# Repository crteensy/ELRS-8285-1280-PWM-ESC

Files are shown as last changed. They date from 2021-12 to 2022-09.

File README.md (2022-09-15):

# ELRS-8285-1280-PWM-ESC
A 2.4 GHz ELRS resceiver with 4 PWM outputs and a 1S, 5A ESC

### Revision 1.1
- should now be more robust with two servos on one channel through a Y cable
 - adjusted pull-up value on PWM1
 - added pull-up on PWM2
- this required a minor layout change for the added pull-up

### Overview:
- 2.4 GHz ExpressLRS receiver, ESP8285 based, with WiFi antenna
- 4 Servo PWM outputs
- on-board ESC
 - Up to 5.5 V input voltage (1S LiPo or HV-LiPo)
 - BLHeli_S I_H_40 (I didn't test if deadtime can be reduced - it probably can)
 - Handled 5 A for over a minute on the bench without damage: bench power supply set to 4.5 V, Mamba 1408 4000KV, HQProp DP 4x3x3. There was a cover over the ESC to reduce airflow from the prop.
- Voltage divider to measure battery voltage (not yet supported by ExpressLRS, 20211230)
- Testpads to flash ESC firmware through the EFM8's UART - can also be used with an external flight controller and serial passthrough to configure the ESC and re-flash it
- ExpressLRS can be flashed through the servo header

RCGroups discussion thread: https://www.rcgroups.com/forums/showthread.php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

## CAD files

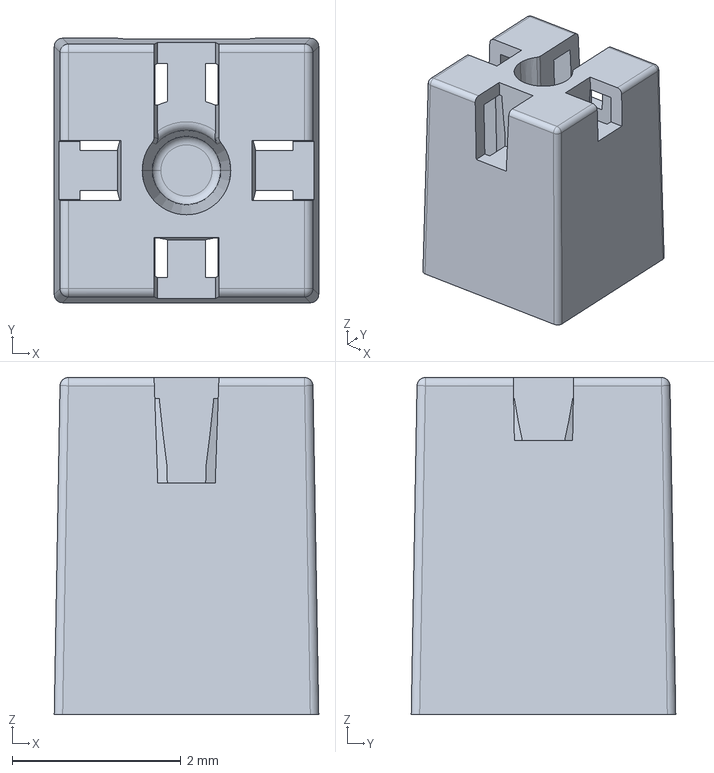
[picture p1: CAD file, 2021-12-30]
3d_local/479480001.stp
3.14 x 3.14 x 4.00 mm

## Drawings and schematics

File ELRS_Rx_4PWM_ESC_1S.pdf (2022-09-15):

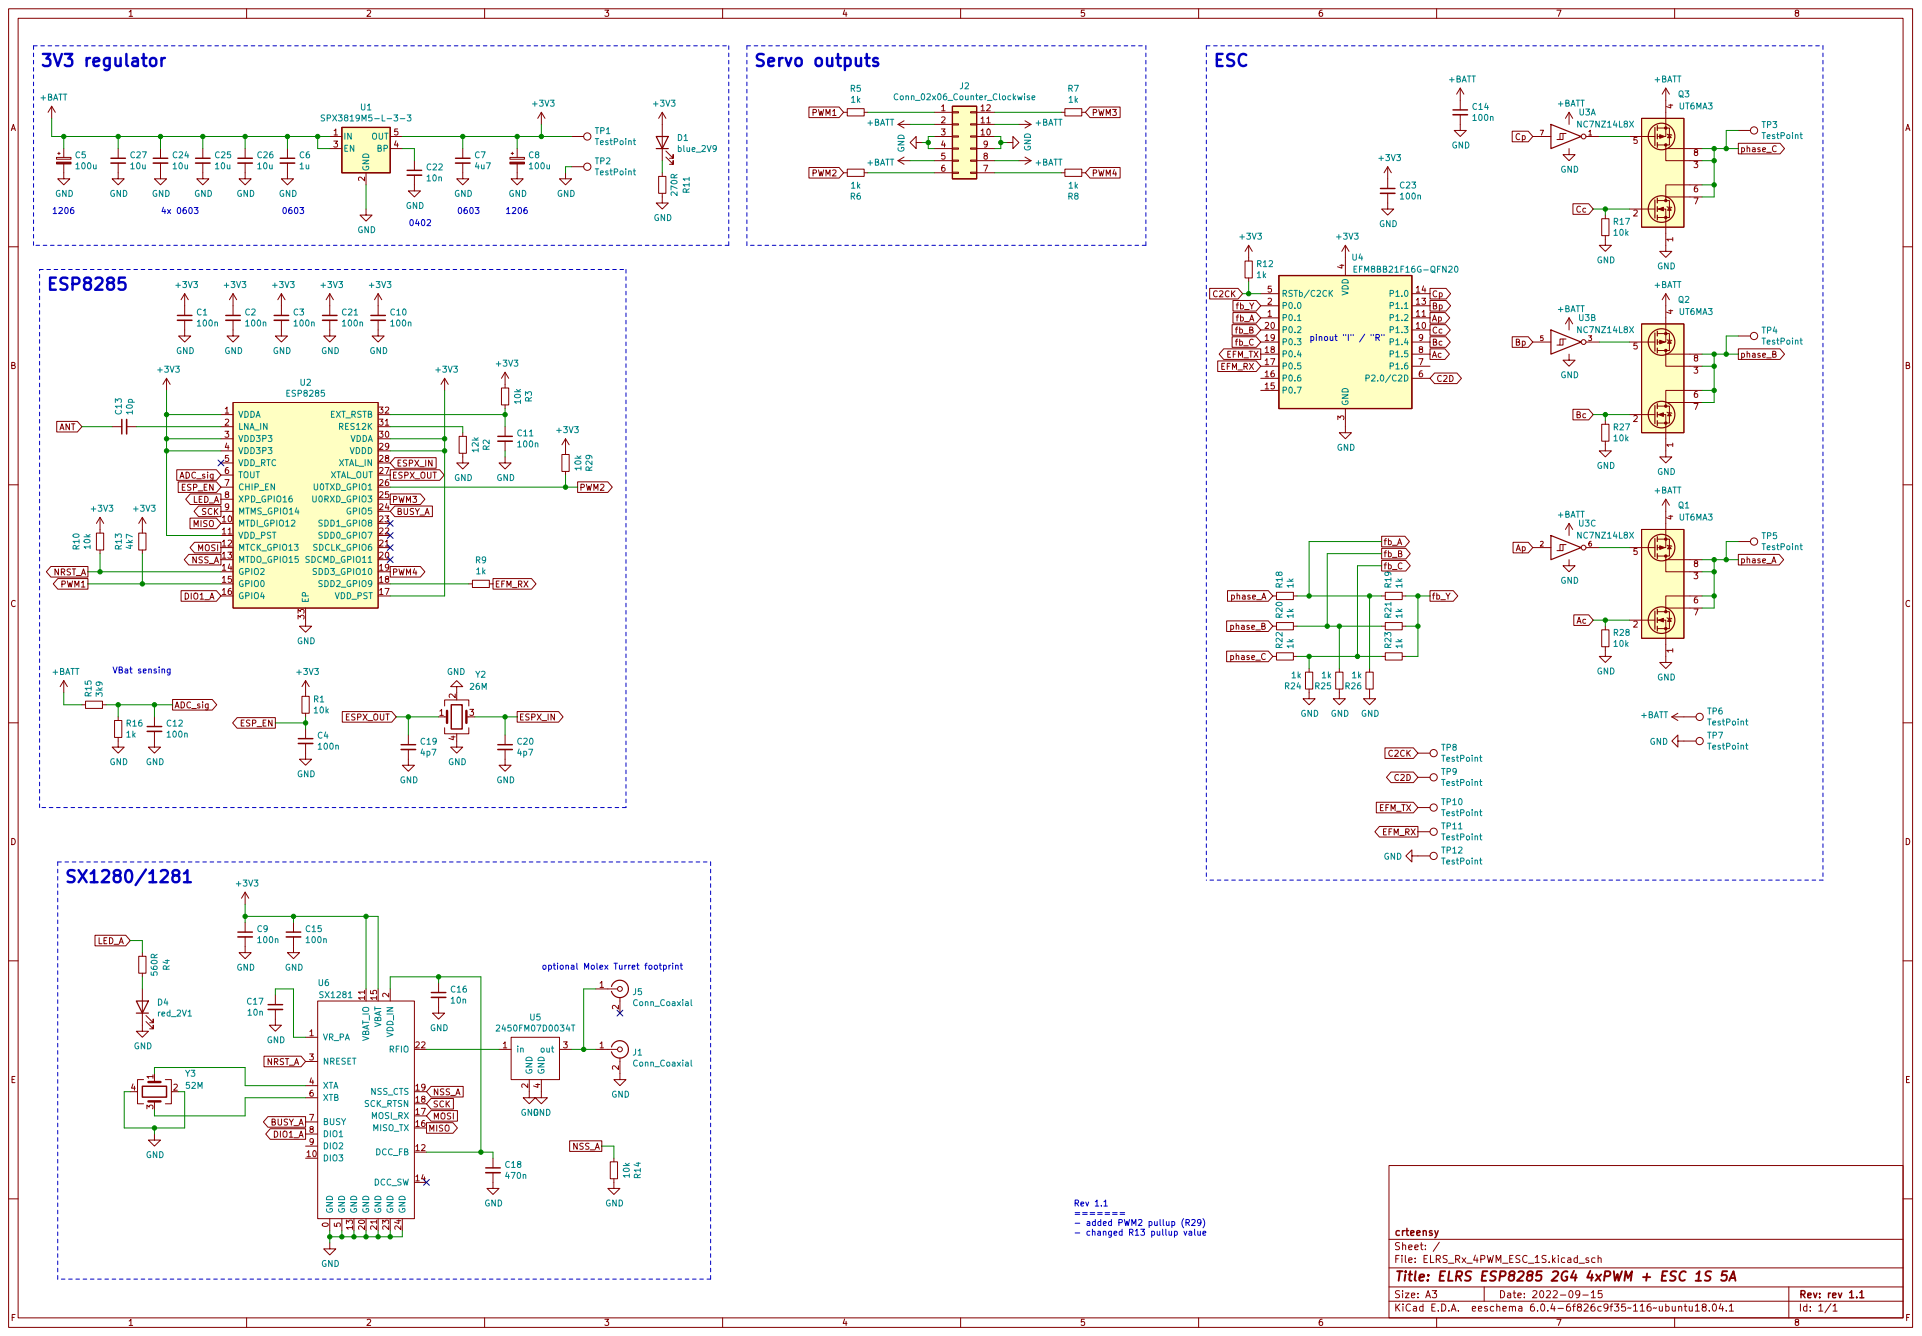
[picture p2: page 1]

optional Molex Turret footprint

2 GND 20 GND 21 RFIO 22 GND 23 GND 24 NRESET 3 XTA 4 GND

Id: 1/1 Title: ELRS ESP8285 2G4 4xPWM + ESC 1S 5A

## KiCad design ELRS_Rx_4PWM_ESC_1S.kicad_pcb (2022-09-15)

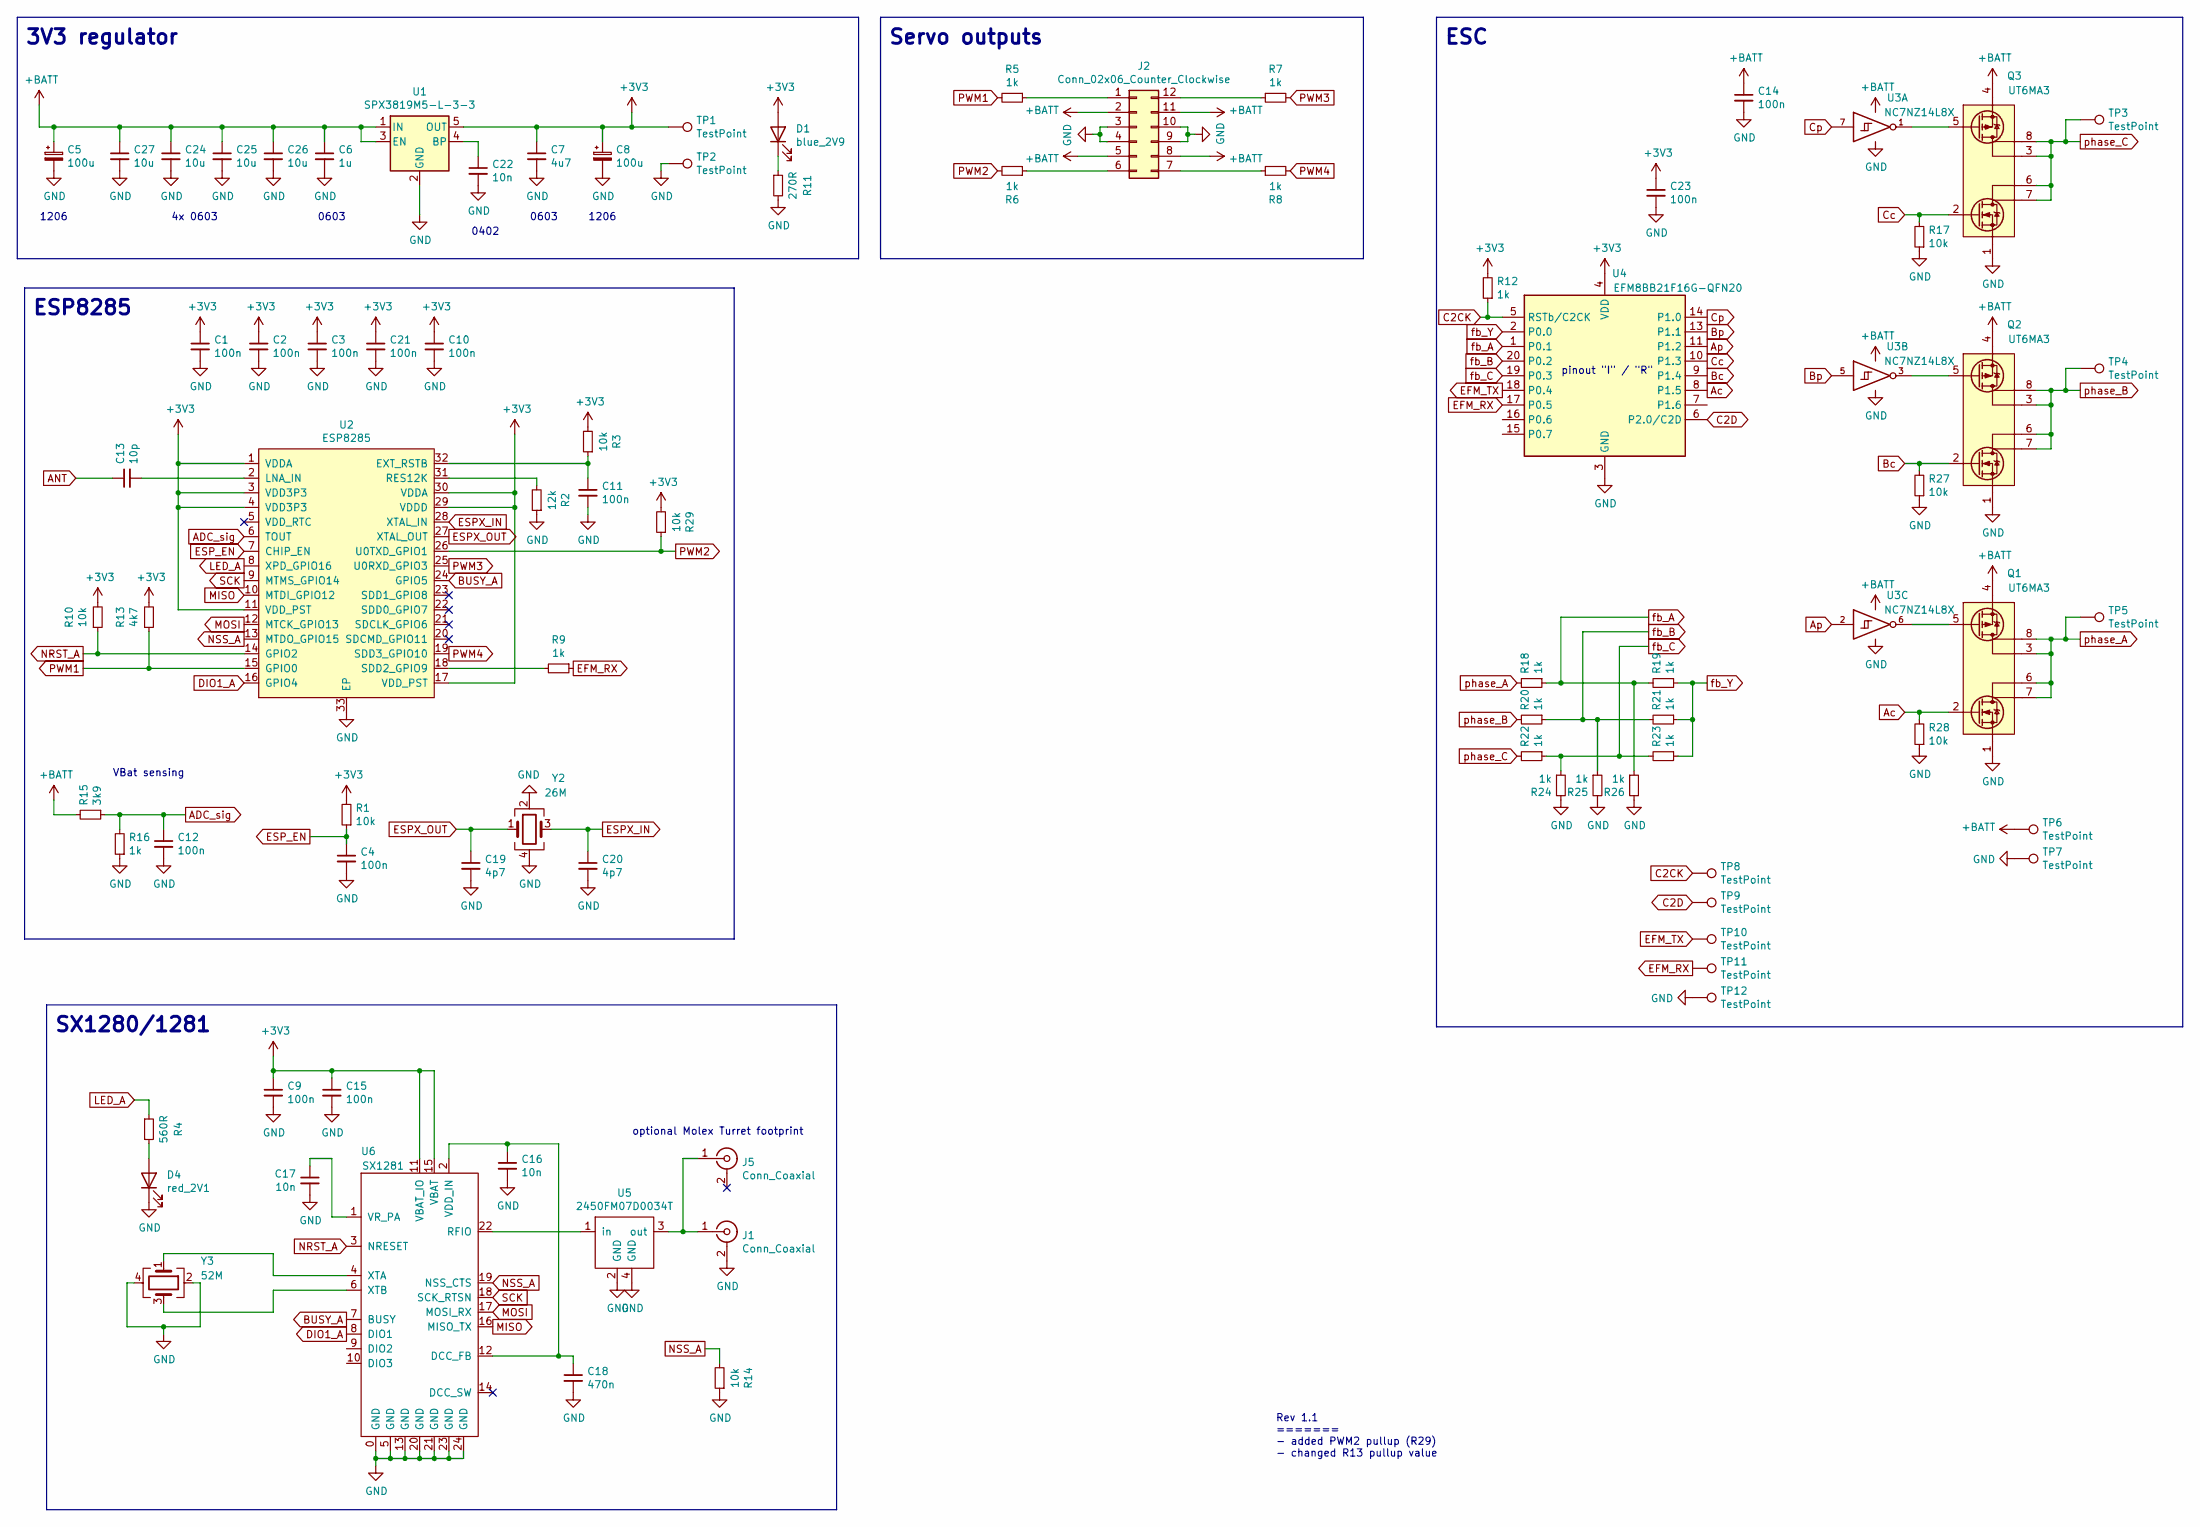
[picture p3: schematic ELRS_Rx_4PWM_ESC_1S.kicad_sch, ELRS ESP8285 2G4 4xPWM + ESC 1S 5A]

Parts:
C1, C2, C3, C4, C9, C10, C11, C12, C14, C15, C21, C23: 100n; C_0402_1005Metric
C5, C8: 100u; CP_EIA-3216-18_Kemet-A
C6: 1u; C_0603_1608Metric
C7: 4u7; C_0603_1608Metric
C13: 10p; C_0402_1005Metric
C16, C17, C22: 10n; C_0402_1005Metric
C18: 470n; C_0402_1005Metric
C19, C20: 4p7; C_0402_1005Metric
C24, C25, C26, C27: 10u; C_0603_1608Metric
D1: blue_2V9; LED_0402_1005Metric
D4: red_2V1; LED_0402_1005Metric
J1: Conn_Coaxial; U.FL_Molex_MCRF_73412-0110_Vertical_dense
J2: Conn_02x06_Counter_Clockwise; BoardEdge_Servo_4
J5: Conn_Coaxial; molex_479480001_2g4-turret
Q1, Q2, Q3: UT6MA3; DFN-6-2EP_2x2mm_P0.65mm_EP2x0.9x0.7
R1, R3, R10, R14, R17, R27, R28, R29: 10k; R_0402_1005Metric
R2: 12k; R_0402_1005Metric
R4: 560R; R_0402_1005Metric
R5, R6, R7, R8, R9, R12, R16, R18, R19, R20, R21, R22, R23, R24, R25, R26: 1k; R_0402_1005Metric
R11: 270R; R_0402_1005Metric
R13: 4k7; R_0402_1005Metric
R15: 3k9; R_0402_1005Metric
TP1, TP2, TP8, TP9, TP10, TP11, TP12: TestPoint; TestPoint_Pad_D1.0mm
TP3, TP4, TP5, TP6, TP7: TestPoint; TestPoint_Pad_2.5x2.5mm
U1: SPX3819M5-L-3-3; SOT-23-5
U2: ESP8285; QFN-32-1EP_5x5mm_P0.5mm_EP3.7x3.7mm_dense
U3: NC7NZ14L8X; UQFN-8_1.6x1.6mm_P0.50mm
U4: EFM8BB21F16G-QFN20; SiliconLabs_QFN-20-1EP_3x3mm_P0.5mm_EP1.8x1.8mm
U5: 2450FM07D0034T
U6: SX1281; QFN-24-1EP_4x4mm_P0.5mm_EP2.6x2.6mm_SX1280_dense
Y2: 26M; Crystal_SMD_2016-4Pin_2.0x1.6mm
Y3: 52M; Crystal_SMD_2016-4Pin_2.0x1.6mm

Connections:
+3V3: C1.1, C2.1, C3.1, C7.1, C8.1, C9.1, C10.1, C15.1, C21.1, C23.1, D1.2 (A), R1.2, R3.2, R10.2, R12.2, R13.2, R29.2, TP1.1, U1.5 (OUT), U2.1 (VDDA), U2.3 (VDD3P3), U2.4 (VDD3P3), U2.11 (VDD_PST), U2.17 (VDD_PST), U2.29 (VDDD), U2.30 (VDDA), U4.4 (VDD), U6.11 (VBAT_IO), U6.15 (VBAT)
+BATT: C5.1, C6.1, C14.1, C24.1, C25.1, C26.1, C27.1, J2.2, J2.5, J2.8, J2.11, Q1.4 (S2), Q2.4 (S2), Q3.4 (S2), R15.2, TP6.1, U1.1 (IN), U1.3 (EN), U3.8 (VCC)
ADC_sig: C12.1, R15.1, R16.2, U2.6 (TOUT)
ANT: C13.1
Ac: Q1.2 (G1), R28.2, U4.8 (P1.5)
Ap: U3.2, U4.11 (P1.2)
BUSY_A: U2.24 (GPIO5), U6.7 (BUSY)
Bc: Q2.2 (G1), R27.2, U4.9 (P1.4)
Bp: U3.5, U4.13 (P1.1)
C2CK: R12.1, TP8.1, U4.5 (RSTb/C2CK)
C2D: TP9.1, U4.6 (P2.0/C2D)
Cc: Q3.2 (G1), R17.2, U4.10 (P1.3)
Cp: U3.7, U4.14 (P1.0)
DIO1_A: U2.16 (GPIO4), U6.8 (DIO1)
EFM_RX: R9.1, TP11.1, U4.17 (P0.5)
EFM_TX: TP10.1, U4.18 (P0.4)
ESPX_IN: C20.1, U2.28 (XTAL_IN), Y2.3
ESPX_OUT: C19.1, U2.27 (XTAL_OUT), Y2.1
ESP_EN: C4.1, R1.1, U2.7 (CHIP_EN)
GND: C1.2, C2.2, C3.2, C4.2, C5.2, C6.2, C7.2, C8.2, C9.2, C10.2, C11.2, C12.2, C14.2, C15.2, C16.2, C17.2, C18.2, C19.2, C20.2, C21.2, C22.2, C23.2, C24.2, C25.2, C26.2, C27.2, D4.1 (K), J1.2 (Ext), J2.3, J2.4, J2.9, J2.10, Q1.1 (S1), Q2.1 (S1), Q3.1 (S1), R2.1, R11.2, R14.1, R16.1, R17.1, R24.2, R25.2, R26.2, R27.1, R28.1, TP2.1, TP7.1, TP12.1, U1.2 (GND), U2.33 (EP), U3.4 (GND), U4.3 (GND), U4.12 (GND), U4.21 (GND), U5.2 (GND), U5.4 (GND), U6.0 (GND), U6.5 (GND), U6.13 (GND), U6.20 (GND), U6.21 (GND), U6.23 (GND), U6.24 (GND), Y2.2, Y2.4, Y3.2, Y3.4
LED_A: R4.1, U2.8 (XPD_GPIO16)
MISO: U2.10 (MTDI_GPIO12), U6.16 (MISO_TX)
MOSI: U2.12 (MTCK_GPIO13), U6.17 (MOSI_RX)
NRST_A: R10.1, U2.14 (GPIO2), U6.3 (NRESET)
NSS_A: R14.2, U2.13 (MTDO_GPIO15), U6.19 (NSS_CTS)
unnamed: C11.1, R3.1, U2.32 (EXT_RSTB)
unnamed: C13.2, U2.2 (LNA_IN)
unnamed: C16.1, C18.1, U6.2 (VDD_IN), U6.12 (DCC_FB)
unnamed: C17.1, U6.1 (VR_PA)
unnamed: C22.1, U1.4 (BP)
unnamed: D1.1 (K), R11.1
unnamed: D4.2 (A), R4.2
unnamed: J1.1 (In), J5.1 (In), U5.3 (out)
unnamed: J2.1, R5.1
unnamed: J2.6, R6.1
unnamed: J2.7, R8.1
unnamed: J2.12, R7.1
unnamed: Q1.5 (G2), U3.6
unnamed: Q2.5 (G2), U3.3
unnamed: Q3.5 (G2), U3.1
unnamed: R2.2, U2.31 (RES12K)
unnamed: R9.2, U2.18 (SDD2_GPIO9)
unnamed: U5.1 (in), U6.22 (RFIO)
unnamed: U6.4 (XTA), Y3.1
unnamed: U6.6 (XTB), Y3.3
PWM1: R5.2, R13.1, U2.15 (GPIO0)
PWM2: R6.2, R29.1, U2.26 (U0TXD_GPIO1)
PWM3: R7.2, U2.25 (U0RXD_GPIO3)
PWM4: R8.2, U2.19 (SDD3_GPIO10)
SCK: U2.9 (MTMS_GPIO14), U6.18 (SCK_RTSN)
fb_A: R18.1, R19.2, R26.1, U4.1 (P0.1)
fb_B: R20.1, R21.2, R25.1, U4.20 (P0.2)
fb_C: R22.1, R23.2, R24.1, U4.19 (P0.3)
fb_Y: R19.1, R21.1, R23.1, U4.2 (P0.0)
phase_A: Q1.3 (D2), Q1.6 (D1), Q1.7 (D1), Q1.8 (D2), R18.2, TP5.1
phase_B: Q2.3 (D2), Q2.6 (D1), Q2.7 (D1), Q2.8 (D2), R20.2, TP4.1
phase_C: Q3.3 (D2), Q3.6 (D1), Q3.7 (D1), Q3.8 (D2), R22.2, TP3.1

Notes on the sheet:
Rev 1.1 ======= - added PWM2 pullup (R29) - changed R13 pullup value
optional Molex Turret footprint
1206
3V3 regulator
ESP8285
0603
pinout "I" / "R"
SX1280/1281
0402
VBat sensing
ESC
4x 0603
Servo outputs

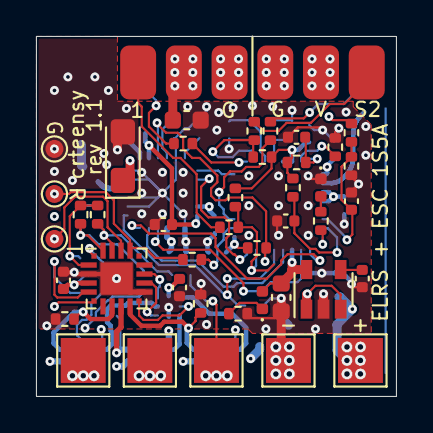
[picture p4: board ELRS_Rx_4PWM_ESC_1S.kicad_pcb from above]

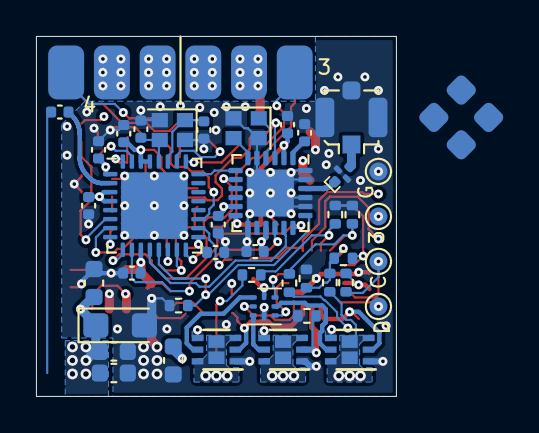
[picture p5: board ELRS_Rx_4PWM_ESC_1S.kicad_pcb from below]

Board: 4 copper layers, 20.0 x 20.0 mm, 84 parts (42 on the bottom side), 56 nets.

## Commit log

2021-12-30 initial commit (kicad, readme)
    [479480001.stp, ELRS_Rx_4PWM_ESC_1S-rev0.2.kicad_pcb, ELRS_Rx_4PWM_ESC_1S.kicad_pcb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]
2021-12-30 minor layout fix
    [ELRS_Rx_4PWM_ESC_1S.kicad_pcb]
2022-09-15 V1.1 adjust pull-up resistors and layout
    [ELRS_Rx_4PWM_ESC_1S.kicad_pcb, ELRS_Rx_4PWM_ESC_1S.kicad_sch, ELRS_Rx_4PWM_ESC_1S_rev1.0.kicad_pcb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]
2022-09-15 fix top silkscreen
    [ELRS_Rx_4PWM_ESC_1S.kicad_pcb]
